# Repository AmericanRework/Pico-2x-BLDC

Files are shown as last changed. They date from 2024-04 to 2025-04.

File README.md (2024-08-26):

# Dual BLDC Controller
One RP2040 Pico drives two brushless motors! Uses SimpleFOC + Halls + TO-220 mosfets or IGBTs. Trying for low cost + lots of flexibility + solder it yourself at home + repairable. Works as a 3x DC motor controller as well.

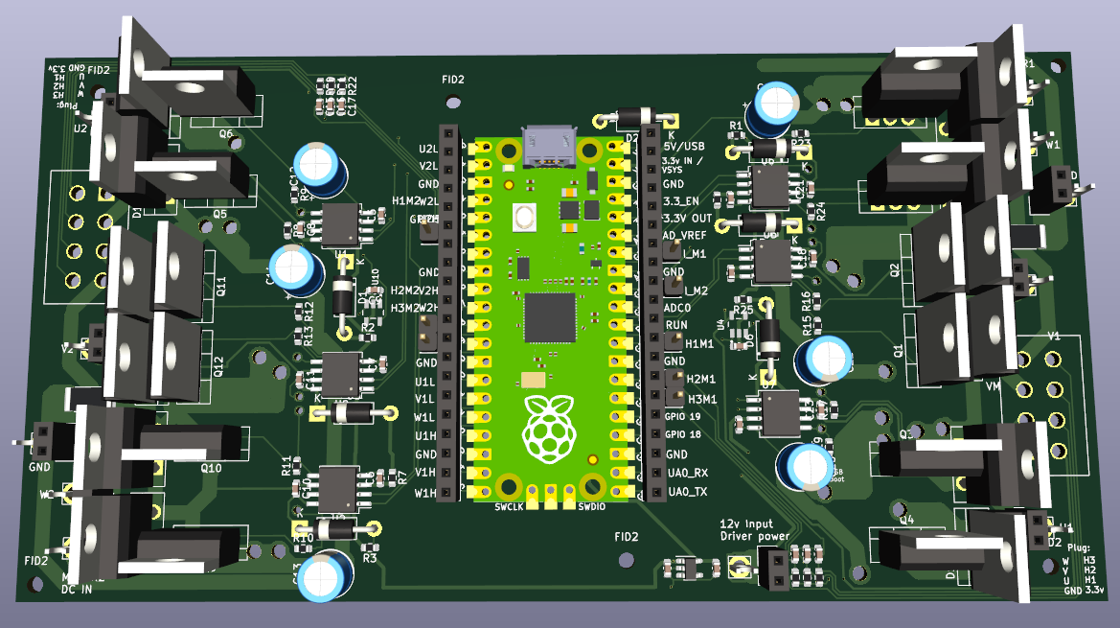
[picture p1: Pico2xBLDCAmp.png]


**Features:**

RP2040 Pico running Simplefoc (https://simplefoc.com/) and using halls (or -untested but should be possible- encoders) for motor commutation. (No FOC - RP2040 doesn't have enough A/D channels for 2x motor FOC.) Current sensing: 1 A/D channel and shunt resistor per motor. Uses 2304 half-H drivers. Can assemble only half the board if you only want one servo amp / want more pico I/O's. Spot for big diodes if you want 'em - Big motors seem to eat my mosfet body diodes rather quickly and IGBT's don't have body diodes. 

Control via usb serial or hardware serial. I2C, SPI, and software CAN might work but are untested. Serial is Human readable, following the simplefoc commander schema: AE1 enables motor, A10 sets motor A to 10 rev/sec, A0 stops motor A. AE0 quickly drops power to motor a. etc... B10 sets motor B to 10 rev/sec... etc... This allows you to control, test, and modify this servo amp right from the Arduino IDE or pretty much anything with a USB port or serial port.

Boards have a spot for molex plugs that are pin compatible with Husqvarna 450x automower drive motors. (NOT the cut motor - it's a different pinout but you can re-pin the cut motor - see additionalNotes.txt) 

Board requires your motor power DC source, and ~12vdc@ say 50mA. The board can either make 3.3v for the RP2040 pico, or you can provide external 3.3v. 

There's a very simple heartbeat signal in the code - if the amp doesn't get an instruction from serial it'll shut down, or delete that line to go forever!

**Assembly/Setup:**

Boards require SMD paste soldering and normal soldering to build: 

- SMD: It's not bad, order a solder mask when you order the board, place components, toaster oven for 3 mins. All SMD components are on the same side of the board. No tiny SMD stuff like the rp2040 chip itself - that's why we use a pico. All diodes are NOT SMD so you can tell which direction they go. (I can never see the tiny lines.) 
- Normal Soldering: in particular the mosfets. They are TO-220 because you are a hacker. You can solder in mosfets you have laying around and then de-solder them yourself to put better ones in. Or put in 3x0.1" pin headers so you can just plug in mosfets when you inevitably dead short them after trying to roll your own 3 phase driver. Basically you might want to 1. swap mosfets lots as you scratch write a 3phase driver. 2. use whatever mosfets are around. 3. repair it yourself. All of these would wreck a normal board but here you can just break out your trusty soldering iron and fix this board instead of throwing it in the trash!
- Make sure you order 2oz copper board so you get thick traces and can use higher current.

Assembled board:
plot

If you don't want to use the A/D (or want to repurpose any other inputs/outputs after you get a board) you can cut the trace to that pin(ehhh. update. not all the traces can be cut. is on hit list for next version), and there's a tinned hole for you to take over. And again, you don't have to build both servo amps if you want more IO's. 

'Firmware' for the rp2040 has some basic configuration and setup instructions in comments at the top of the code. It's pretty well tested and has been running on 2 boards for months without failing on an automower. Open up Arduino ide, install libraries: SimpleFOC, SimpleFOC drivers, and the Earle Philhower rp2040 core, compile and upload to your pico, good to go. Check top of the firmware file (RP2040SFocAmp.ino) for various additional documentation that might help you get started. 

There are two other firmware versions - one example for 3x DC motors, and one old version based on (https://github.com/ClemensElflein/xESC2040/tree/main/firmware/src) that does not use simplefoc. Both 'other' firmware versions need their pins.h file checked to be sure they follow the current board pico pin assignments, but should be somewhat functional other than that afaik. Let's call them good starting points. 

**Tested**

Tested using velocity control and torque control up to 10A/21v. You'll want heatsinks and low rdson mosfets to get to 10A. Tested the half-h drivers with igbts and better mosfets on a big inductive load to 60V, will update as we test more. Two boards are running in a Husqvarna 450x Automower as I write this. Maybe 10 hours of operation so far. Will update if/when anything fails. Update: ~100hrs of mowing, 0 servo amp faults/problems. Will still update if/when anything fails.

2 amps, 3 motors. One board has both drive motors, one has the cut motor.
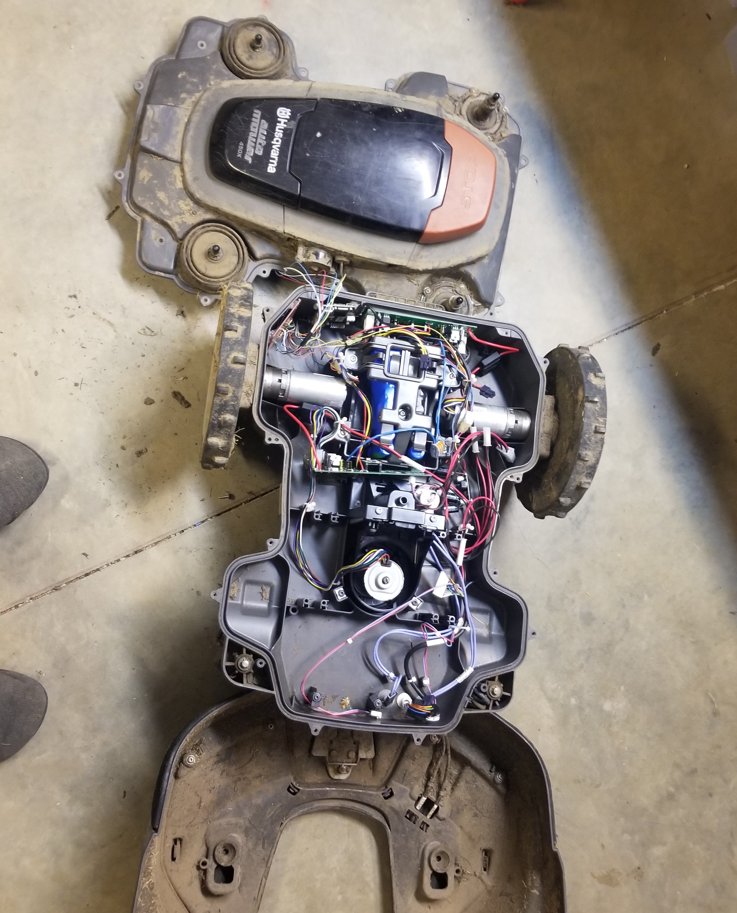
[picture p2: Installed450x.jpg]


Tested with 3x brushed (non 3 phase) motors using https://github.com/simplefoc/Arduino-FOC-dcmotor  - worked great but I did not test feedback, just that it could spin the motors. Off the top of my head there's only enough pico pins for 2x quadrature encoders.

**Thank you:**

Big thank you to https://github.com/ClemensElflein/ for creating the Open Mower project and his very well thought out 3 phase rp2040 servo amp code. His project inspired me to take the leap and make this happen. The original plan was use the openmower framework to control this servo amp, again - the amp plugs right into 450X automower drive motors, no hacking required. This board could(at least used to!) run (a version of?) the Xesc2040 servo amp code. Creating a firmware for this board that allows it to connect to openmower would be cool but I ended up writing a very simple mower controller instead.

SimpleFOC is absolutely brilliant. Can't recommend enough. If you are making bldc controllers they are a great place to start! (https://simplefoc.com/)

RP2040 / Pi Pico + Earle Philhower core (https://github.com/earlephilhower/arduino-pico) has been rock solid and a joy to work on. 

Thanks to everyone who open sources their work - makes the world a better place. Hope my code helps you!

**Plans/Stuff that's broken, rough order:**

- Current sense is at best not super calibrated, at worst needs work. Functions well enough to shut down the amp if current limit is hit.
- Test both DC and BLDC motors with an encoder instead of halls.
- Build more robots using this amp.
- Test it up to 240vdc/10A. Should work?
- When you disable a moving simplefoc motor with an 'AE0', it'll try to jump back to that velocity when you re-enable it. Might be fixed in newest simplefoc version or maybe it's something I did. Low priority 'cause it just spins a wheel a bit when you re-enable. Could be much a bigger problem on say a robot arm or CNC with a hard stop.
- Connect JUST the 2304's to a Mesa FPGA board running linuxCNC. Yep. Dump the pico and put your own brain on these drivers.
- I2C should work via pico pins GP17 and GP16. I think there is also now software CAN for the 2040 - loose 25% or so of one core but get CAN. Should be able to get it working. SPI is also exposed on pins 16/17/18/19 but again is untested. 

**Next board iteration:**

- Going to be a while. I've got enough of these boards for my next couple years of planned projects. Maybe...2027 or so we'll fix this stuff and anything else that shows up. Only thing that will trigger a sooner update is if high voltage or DC motor mode doesn't work.
- Heat sinks: Mosfet locations are not in a nice line. We've got 1 sink per mosfet, and once we start using more power we might want some real cooling here not just tiny heat sinks to air. Is it worth the pain of moving everything? Eh... Maybe. Might be easier to just machine the right pockets/holes into an aluminum block. 
- Delete the onboard 3.3v - Turns out you're not supposed to use linear regulators as DC-DC converters. Oops. It works but wastes 40mA+. Delete it 'cause 3.3v or 5v can come from RPi or BBB or pretty much any other board you use to drive this. AND if you have external 3.3v you can dump power to the pico even if you leave the DC main power connected.
- Redo pico io mapping so that each half-H is on it's own PWM slice.
- Motor 1 half-h cutable-traces: if you cut the top side trace between the pico and the tinned hole, remain connected to their half-h because traces went straight to the pico pins. 
- Make the power input and GND holes large enough to accommodate 12Ga wire.
- Fix various labels on the board. FID2 looking at you. Also most of the Motor 2 labels.

Cheers!
-American Rework

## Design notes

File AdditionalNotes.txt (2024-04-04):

Additional documentation:

To connect external 3.3v: use the 3.3v in / vsys pin (upper right corner of the pico if usb is top) It's labeled on the board.

Pinout for Husqvarna Automower 450x cut motor to match the drive motor 8 pin molex (drive motor comes with a 10 pin molex but only 8 pins used): 

-Plug latch on top. View looking at circuit board/back of plug:
-First row: black-gnd, blue-U, white-V, green-W
-Second row: red-3.3v, yellow-hallU, grey-hallV, purple-hallW

Gives same electrical angle as the drive motors. Our pinout is written directly on the board to make wiring up motors easy.

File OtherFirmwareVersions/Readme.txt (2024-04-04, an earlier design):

The RP2040BLDCAttempt2 firmware WILL NOT WORK on the current version of the board. Grab the new version of pins.h from the /firmware folder and you might be good. No promises though.

It is only an example/starting point if you want to roll your own servo amp and not use simplefoc. 

RP2040SimpleDC3xMTR has run 3x DC motors. Check the pins.h file just to be sure. I haven't tested it recently but it's probably ok. I have a project coming up where I need to control some DC motors so this might get updated in the next year or two. Heh.

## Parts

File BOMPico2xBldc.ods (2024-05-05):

Digikey Part # | Mfg Part # | Description | Qty | Cost | Line Cost | Notes | Total Cost
2648-SC0915CT-ND | SC0915 or SC0917 | Raspberry Pi Pico | 1 | 5 | 5 |  | 38.074
You Choose. |  | Power FET or IGBT | 12 | 0.87 | 10.44 | I have been quite happy with DMT6009LCT mosfets – Rdson 12mOhm, N-Channel 60 V 37.2A (Tc) 2.2W (Ta), 25W (Tc) Through Hole TO-220-3
 | SURF1060 | Big Flyback diode | 12 | 0.57 | 6.84 | Or try using mosfet body diodes. These have been pretty bulletproof so far: 10A / 600v.
DGD2304S8-13DICT-ND | DGD2304S8-13 | Gate driver | 6 | 1.2 | 7.2
RHM.001AUCT-ND | PMR100HZPFV1L00 | Current shunt resistor | 2 | 0.54 | 1.08
1276-1935-1-ND |  | .1uF SMD Cap | 14 | 0.018 | 0.252
1276-1062-1-ND |  | 470nF/16V Cap | 6 | 0.044 | 0.264 | boost caps – must upgrade for higher mains.
 |  | 2.2uF/400V | 6 |  | 0 | Mains caps
1276-1096-2-ND |  | 10uF/16V Cap | 2 | 0.1 | 0.2 | 1@ 12v and 1@ 3.3v
 | Diode:UF4007 | UF4007 Diode | 6 |  | 0
 | Diode:1N5817 | 1N5817 Shottkey Diode | 1 |  | 0
WM3583-ND | Molex 874270842 | Motor plug | 2 | 2.02 | 4.04 | Don't forget motor side of these and the pins.
 | Connector_PinSocket_2.54mm:PinSocket_1x20_P2.54mm_Vertical | Conn_01x20_Pin | 0 |  | 0 | Only if you are going to plug the pico in.
P10GCT-ND |  | 10 Resistor | 18 | 0.028 | 0.504
311-2.20KHRCT-ND |  | 2k2 Resistor | 6 | 0.019 | 0.114
696-1834-1-ND |  | 1mR Resistor | 2 | 0.67 | 1.34
296-47654-1-ND | INA180A3 | INA180A4 Currrent shunt Amplifier | 2 | 0.4 | 0.8
31-AP7383-33W5-7CT-ND |  | Unused: 3.3V Linear Regulator | 0 | 0.41 | 0 | Use external 3.3v so you can drop power to the pico remotely. Also, linear regulators aren't dc-dc buck converters lol....

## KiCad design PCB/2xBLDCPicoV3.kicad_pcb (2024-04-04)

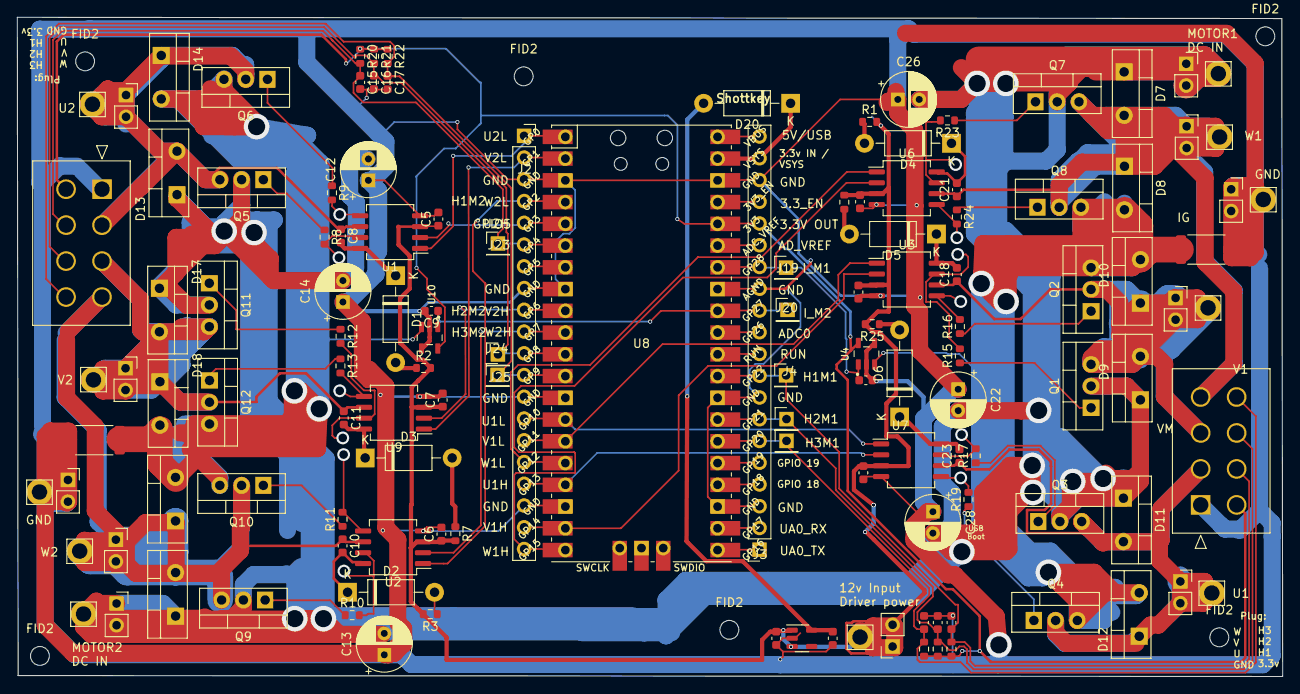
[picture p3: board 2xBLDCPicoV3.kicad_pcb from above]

Board: 4 copper layers, 147.8 x 77.0 mm, 124 parts (0 on the bottom side), 88 nets.

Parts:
C1, C5, C6, C7, C19, C27: 100nF; C_0603_1608Metric
C2, C3, C4, C9, C15, C16, C17, C20: .1uF; C_0603_1608Metric
C8, C10, C11, C18, C21, C23: 470nF/16V; C_0603_1608Metric
C12, C26: 2.2uF/400V; CP_Radial_D6.3mm_P2.50mm
C13, C14, C22, C28: 2.2uF/400v; CP_Radial_D6.3mm_P2.50mm
C24, C25: 10uF/16V; C_0603_1608Metric
D1, D2, D3, D4, D5, D6: UF4007; D_DO-41_SOD81_P10.16mm_Horizontal
D7, D8, D9, D10, D11, D12, D13, D14, D15, D16, D17, D18: C3D10060A; TO-220-2_Vertical
D20: 1N5817; D_DO-41_SOD81_P10.16mm_Horizontal
FID2, FID2#2, FID2#3, FID2#4, FID2#5, FID2#6: MTG Hole; MountingHole_2.2mm_M2
J1, J22: 874270842; CON_874270842
J2, J3: Conn_01x20_Pin; PinSocket_1x20_P2.54mm_Vertical
J4, J5, J7, J19, J20, J23, J24, J25: Conn_01x01_Pin; PinHeader_1x01_P2.54mm_Vertical
J6, J8, J9, J10, J11, J12, J13, J15, J16, J17, J18: Conn_01x02; PinSocket_1x02_P2.54mm_Vertical
Q1, Q2, Q3, Q4, Q5, Q6, Q11, Q12: IRF540N; TO-220-3_Vertical
Q7, Q8, Q9, Q10: STGP10NC60H; TO-220-3_Vertical
R1, R2, R3, R7, R8, R9, R10, R11, R12, R13, R15, R16, R17, R19, R23, R24, R25, R26: 010; R_0603_1608Metric
R4, R5, R6, R20, R21, R22: 2k2; R_0603_1608Metric
R14, R18: 1mR; R_2512_6332Metric
U1, U2, U3, U6, U7, U9: IRS2304; SO-8_5.3x6.2mm_P1.27mm
U4, U10: INA180A4; SOT95P280X145-5N
U5: XC6220B331MR; SOT-23-5
U8: Pico; RPi_Pico_SMD_TH

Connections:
+3V3: C25.1, D20.2 (A), U5.5 (VOUT)
+12V: C1.1, C5.1, C6.1, C7.1, C19.1, C24.1, C27.1, J11.1, J11.2, R1.2, R2.2, R3.2, R7.2, R25.2, R26.2, U1.3 (VCC), U2.3 (VCC), U3.3 (VCC), U5.1 (VIN), U5.3 (CE), U6.3 (VCC), U7.3 (VCC), U9.3 (VCC)
/+3.3V to Sensors: J1.5, J22.5, R4.1, R5.1, R6.1, R20.1, R21.1, R22.1
/HALL1: C2.1, J1.6, J4.1, R4.2
/HALL1M2: C15.1, J22.6, J23.1, R20.2
/HALL2: C3.1, J1.7, J5.1, R5.2
/HALL2M2: C16.1, J22.7, J24.1, R21.2
/HALL3: C4.1, J1.8, J7.1, R6.2
/HALL3M2: C17.1, J22.8, J25.1, R22.2
/MCU/+3.3V to Sensors: J3.16, U8.36 (3V3)
/MCU/ADCINSPARE1: J3.11, U8.31 (GPIO26_ADC0)
/MCU/CURRENT_SENSE: C20.1, J3.14, J19.1, U4.1 (OUT), U8.34 (GPIO28_ADC2)
/MCU/CURRENT_SENSEM2: C9.1, J3.12, J20.1, U8.32 (GPIO27_ADC1), U10.1 (OUT)
/MCU/HALL_1: J3.9, U8.29 (GPIO22)
/MCU/HALL_2: J3.7, U8.27 (GPIO21)
/MCU/HALL_2M2: J2.11, U8.11 (GPIO8)
/MCU/HALL_3: J3.6, U8.26 (GPIO20)
/MCU/HALL_3M2: J2.12, U8.12 (GPIO9)
/MCU/Hall_1_M2 / i2c0 SDA / UART1_TX: J2.6, U8.6 (GPIO4)
/MCU/Spare1/spi0 TX/i2c1 SCL: J3.5, U8.25 (GPIO19)
/MCU/Spare2/spi0 SCK/i2c1 SDA: J3.4, U8.24 (GPIO18)
/MCU/Spare3 / i2c0 SCL UART1_RX: J2.7, U8.7 (GPIO5)
/MCU/U1H: J2.17, U7.2 (HIN), U8.17 (GPIO13)
/MCU/U1L: J2.14, U7.1 (LIN), U8.14 (GPIO10)
/MCU/U2H: J2.5, U1.2 (HIN), U8.5 (GPIO3)
/MCU/U2L: J2.1, U1.1 (LIN), U8.1 (GPIO0)
/MCU/UART0_RX /spi0 Csn / I2C0 SCL: J3.2, U8.22 (GPIO17)
/MCU/UART0_TX /spi0 RX / I2C0 SDA: J3.1, U8.21 (GPIO16)
/MCU/V1H: J2.19, U3.2 (HIN), U8.19 (GPIO14)
/MCU/V1L: J2.15, U3.1 (LIN), U8.15 (GPIO11)
/MCU/V2H: J2.9, U8.9 (GPIO6), U9.2 (HIN)
/MCU/V2L: J2.2, U8.2 (GPIO1), U9.1 (LIN)
/MCU/W1H: J2.20, U6.2 (HIN), U8.20 (GPIO15)
/MCU/W1L: J2.16, U6.1 (LIN), U8.16 (GPIO12)
/MCU/W2H: J2.10, U2.2 (HIN), U8.10 (GPIO7)
/MCU/W2L: J2.4, U2.1 (LIN), U8.4 (GPIO2)
/PowerM1/HSW: R23.2, U6.7 (HO)
/PowerM1/IGBT_GND: D8.2 (A), D10.2 (A), D12.2 (A), Q2.3 (S), Q4.3 (S), Q8.3 (S), R18.1, U4.3 (IN+)
/PowerM1/LSW: R24.2, U6.5 (LO)
/PowerM2/HSW: R10.2, U2.7 (HO)
/PowerM2/IGBT_GND: D14.2 (A), D16.2 (A), D18.2 (A), Q6.3 (S), Q10.3 (S), Q12.3 (S), R14.1, U10.3 (IN+)
/PowerM2/LSW: R11.2, U2.5 (LO)
/PowerM2/U_To_PlugM2: C8.1, D13.2 (A), D14.1 (K), J18.1, J18.2, Q5.3 (S), Q6.2 (D), U1.6 (VS)
/PowerM2/VM2: C12.2, C13.2, C14.2, D13.1 (K), D15.1 (K), D17.1 (K), J15.1, J15.2, Q5.2 (D), Q9.2 (D), Q11.2 (D)
/PowerM2/V_To_PlugM2: C11.1, D17.2 (A), D18.1 (K), J17.1, J17.2, Q11.3 (S), Q12.2 (D), U9.6 (VS)
/PowerM2/W_To_PlugM2: C10.1, D15.2 (A), D16.1 (K), J16.1, J16.2, Q9.3 (S), Q10.2 (D), U2.6 (VS)
/U_To_Plug: C23.1, D11.2 (A), D12.1 (K), J1.2, J9.1, J9.2, Q3.3 (S), Q4.2 (D), U7.6 (VS)
/VM: C22.2, C26.2, C28.2, D7.1 (K), D9.1 (K), D11.1 (K), J10.1, J10.2, Q1.2 (D), Q3.2 (D), Q7.2 (D)
/V_To_Plug: C18.1, D9.2 (A), D10.1 (K), J1.3, J6.1, J6.2, Q1.3 (S), Q2.2 (D), U3.6 (VS)
/W_To_Plug: C21.1, D7.2 (A), D8.1 (K), J1.4, J8.1, J8.2, Q7.3 (S), Q8.2 (D), U6.6 (VS)
GND: C1.2, C2.2, C3.2, C4.2, C5.2, C6.2, C7.2, C9.2, C12.1, C13.1, C14.1, C15.2, C16.2, C17.2, C19.2, C20.2, C22.1, C24.2, C25.2, C26.1, C27.2, C28.1, J1.1, J2.3, J2.8, J2.13, J2.18, J3.3, J3.8, J3.13, J3.18, J12.1, J12.2, J13.1, J13.2, J22.1, R14.2, R18.2, U1.4 (COM), U2.4 (COM), U3.4 (COM), U4.2 (GND), U4.4 (IN-), U5.2 (GND), U6.4 (COM), U7.4 (COM), U8.3 (GND), U8.8 (GND), U8.13 (GND), U8.18 (GND), U8.23 (GND), U8.28 (GND), U8.33 (AGND), U8.38 (GND), U9.4 (COM), U10.2 (GND), U10.4 (IN-)
unnamed: D1.2 (A), R2.1
unnamed: C8.2, D1.1 (K), U1.8 (VB)
unnamed: D2.2 (A), R3.1
unnamed: C10.2, D2.1 (K), U2.8 (VB)
unnamed: D3.2 (A), R7.1
unnamed: C11.2, D3.1 (K), U9.8 (VB)
unnamed: D4.2 (A), R1.1
unnamed: C21.2, D4.1 (K), U6.8 (VB)
unnamed: D5.2 (A), R26.1
unnamed: C18.2, D5.1 (K), U3.8 (VB)
unnamed: D6.2 (A), R25.1
unnamed: C23.2, D6.1 (K), U7.8 (VB)
unnamed: D20.1 (K), J3.19, U8.39 (VSYS)
unnamed: J3.10, U8.30 (RUN)
unnamed: J3.15, U8.35 (ADC_VREF)
unnamed: J3.17, U8.37 (3V3_EN)
unnamed: J3.20, U8.40 (VBUS)
unnamed: Q1.1 (G), R15.1
unnamed: Q2.1 (G), R16.1
unnamed: Q3.1 (G), R17.1
unnamed: Q4.1 (G), R19.1
unnamed: Q5.1 (G), R8.1
unnamed: Q6.1 (G), R9.1
unnamed: Q7.1 (G), R23.1
unnamed: Q8.1 (G), R24.1
unnamed: Q9.1 (G), R10.1
unnamed: Q10.1 (G), R11.1
unnamed: Q11.1 (G), R12.1
unnamed: Q12.1 (G), R13.1
unnamed: R8.2, U1.7 (HO)
unnamed: R9.2, U1.5 (LO)
unnamed: R15.2, U3.7 (HO)
unnamed: R16.2, U3.5 (LO)
unnamed: R17.2, U7.7 (HO)
unnamed: R19.2, U7.5 (LO)
unnamed: R12.2, U9.7 (HO)
unnamed: R13.2, U9.5 (LO)

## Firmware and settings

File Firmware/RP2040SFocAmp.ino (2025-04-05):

/*
** Most recent version as of March 2024. Servo amp for Automower!
This is mostly example code from SimpleFOC. Follow their license. 

DO NOT PLUG PICO INTO USB WHILE IT'S INSTALLED /PLUGGED INTO BEAGLEBONE. WILL SEND POSSIBLY 5V DOWN THE BEAGLEBONE 3.3V POWER LINE.

Install: 
use Arduino ide, add packages / boards:
known working:
Simplefoc 2.3.2, SimpleDCmotor 1.0.0 simplefocDrivers 1.0.6, board: Raspi pico rp2040 by Philhower 3.7.2
Testing:
SimpleDCmotor 1.0.2 simplefocDrivers 1.0.7

HAD TO delete rp2040.h under current sense in the standard simplefoc library to get this pwm on rp2040 to work... 2024: No longer have to do this!

future self: to get serial access in linux: usermod -a -G tty myusername
and possibly: sudo gpasswd --add ${USER} dialout


Downloading to a pico:
plug in, check show all devices, look for uf2 devices - may have to select the board type - a rp2040 pico not the mbed version.

Running it:
  to 'command' use ? to list commands. not that useful. but then you can say "AE0" to disable motor A, AE1 ENABLES. 
  A10: 10 Is like set torqe/velocity goal to 10. YEP. STARTING AT 1 OR EVEN LESS IS A GOOD IDEA.

//commander is set to have some extra methods: I, C, H, and V all do extra stuff we add here. Check out commander.h for more stuff you can do!
// I is (re)-init. I still can't get init to run a full alignment cycle but can force various override angles? Probably could fix but just never end up using it.
//C is measure current? I think? 
//H is hall state. Helpful when you are adding halls to a non-hall motor.
//V is current velocity. 
 */

 //motors are currently set to use velocity control - and hopefully negative values go in reverse? we'll see.
 //CONFIRMED! NEGATIVE VELOCITY IS CHANGE DIRECTION. WOO0.

//not sure what happened one time I tried sending A10 B10 and b motor just stopped working. reboot fixed lol...
//YO THIS IS IMPORTANT: Can set to use heartbeat or usb/ hardware serial ports. See below.


//#include <Arduino.h>
#include <SimpleFOC.h>
// software interrupt library
//#include <PciManager.h>
//#include <PciListenerImp.h>
#include <SimpleFOCDrivers.h>
#include "pins.h"


//motor pole pairs = # of permanent magnets in rotor.
BLDCMotor motor = BLDCMotor(11);

BLDCMotor motor2 = BLDCMotor(11);
//BLDCDriver3PWM driver = BLDCDriver3PWM(9, 5, 6, 8);

BLDCDriver6PWM driver = BLDCDriver6PWM(PIN_UH, PIN_UL, PIN_VH, PIN_VL, PIN_WH, PIN_WL);

BLDCDriver6PWM driver2 = BLDCDriver6PWM(PIN_UHM2, PIN_ULM2, PIN_VHM2, PIN_VLM2, PIN_WHM2, PIN_WLM2);

// Stepper motor & driver instance
//StepperMotor motor = StepperMotor(50);
//StepperDriver4PWM driver = StepperDriver4PWM(9, 5, 10, 6,  8);

// hall sensor instance
HallSensor sensor = HallSensor(PIN_HALL_U, PIN_HALL_V, PIN_HALL_W, 11);

int hallu, hallv, hallw = 0; //for manual hall testing.

HallSensor sensor2 = HallSensor(PIN_HALL_UM2, PIN_HALL_VM2, PIN_HALL_WM2, 11);
// Interrupt routine intialisation
// channel A, B and C callbacks


//////////////////////////////////////////////////////////////////////////////////////////
// YO THESE ARE IMPORTANT. SET THEM APPROPRIATELY SO THAT WE ONLY HAVE TO MAINTAIN ONE SERVOAMP CODEBASE.
HardwareSerial* whichSerial = &Serial1; //&Serial for usb or &Serial1 for hardware pins. See pins.h for which pins to use. &Serial2 Should also work but is untested.


//heartbeat:
bool useHeartbeat = true; //true to turn everything off if we dont' hear from coms. 
unsigned long last_heartbeat_millis = 0;
int heartbeat_shutdown_millis = 5000; // 5000 ms = 5 seconds no instruction shut down motors. Yes that's kind of a long time. meh. at least it's there.


void doA(){sensor.handleA();}
void doB(){sensor.handleB();}
void doC(){sensor.handleC();}

void doA2(){sensor2.handleA();}
void doB2(){sensor2.handleB();}
void doC2(){sensor2.handleC();}

//first # is milivolts per ... amp? 
//InlineCurrentSense the_current_sense = InlineCurrentSense(500.0, PIN_CURRENT_SENSE, PIN_CURRENT_SENSE);
//DIY that shit:
float motor1_Current = 0;
float motor1_AvgCurrent = 0;
int debugCounter = 0;

float motor2_Current = 0;
float motor2_AvgCurrent = 0;

// commander interface
//there are zero - ZERO! examples of two motors controlled by the commander. wut!? Maybe I bad at searching. this should be interesting.
// I got AI to spit out an example it claims will send the same command to both motors. ugh. not what I need.
Commander command = Commander(*whichSerial);
void onMotor(char* cmd){ command.motor(&motor, cmd); }
void onMotor2(char* cmd){ command.motor(&motor2, cmd); }

//try to restart a motor? doesn't quite work right. 
void reInit1(char* cmd){ 
  /*
  motor.init();
  motor.target = 0; //wish this was to CMD then you could init @ different power levels woo.
  motor.enable();
  //motor.initFOC(); //this doesn't force a re-align for some reason...
  motor.initFOC(5.236, Direction::CCW);
  */
   }

//OK! after some testing, sampling every loop and adding to a moving average: 
//0 reads 4-10, 0.5 amps reads 165 to 175, 1.5 amps reads 370 to 390, ~ 10A 912-933, ~4 AMPS 616 TO 703.
void readCurrent(char* cmd){ 
  //motor1_Current = the_current_sense.getDCCurrent();
 // motor1_Current = analogRead(PIN_CURRENT_SENSE);
//  *whichSerial.println(motor1_Current);

    whichSerial->println(motor1_AvgCurrent);
    whichSerial->println(motor2_AvgCurrent);
 }

 void printVelo(char* cmd){ 
  whichSerial->println(motor.shaft_velocity);
  whichSerial->println(motor2.shaft_velocity);
 }

void readHalls(char* cmd){ 
  hallu = digitalRead(PIN_HALL_U);
  hallv = digitalRead(PIN_HALL_V);
  hallw = digitalRead(PIN_HALL_W);
  whichSerial->println("HALLS:");
  whichSerial->println(hallu);
  whichSerial->println(hallv);
  whichSerial->println(hallw);
 }



void setup() {

  // initialize encoder sensor hardware
  
  sensor.init();
  sensor.enableInterrupts(doA, doB, doC);
  
   
  sensor2.init();
  sensor2.enableInterrupts(doA2, doB2, doC2);
  


  //COMMENT THIS OUT TOO FOR OPEN LOOP!
  motor.linkSensor(&sensor);

  motor2.linkSensor(&sensor2);


  //CURRENT SENSOR - sfoc version. Doesn't 'just work.' doing my own thing but I'll leave this here maybe help someone. 
  //inlineCurrentSense(resistorValue,gain,AnalogPin#'s) or (mv/amp, analogpins)
  //the_current_sense = InlineCurrentSense(200.0, PIN_CURRENT_SENSE, PIN_CURRENT_SENSE);
  
  //the_current_sense.init();
  // do this not sure if it'll break motor alignment ability:  motor.linkCurrentSense(&current_sense);

  // link current sense and driver
  //current_sense.linkDriver(&driver);
  // link motor and current sense
  //motor.linkCurrentSense(&current_sense);


  //should be able to do this to get DC current:
  //  motor1_Current = current_sense.getDCCurrent();




  // driver config
  // power supply voltage [V]
  driver.voltage_power_supply = 12;
  driver.init();
  driver.dead_zone = 0.1;
  // link driver
  motor.linkDriver(&driver);

  driver2.voltage_power_supply = 12;
  driver2.init();
  driver2.dead_zone = 0.1;
  // link driver
  motor2.linkDriver(&driver2);



  // choose FOC modulation OPEN LOOP TO TEST A MOTOR? SEE THE BLDC ATTEMPT #5 FOR WORKING OPEN LOOP
 // motor.foc_modulation = FOCModulationType::SinePWM;
  // set control loop type to be used
 //motor.controller = MotionControlType::velocity_openloop;

 
 motor.phase_resistance = 1.8;
 motor.current_limit = 3.0;
 motor.KV_rating = 100; //RPM'S PER VOLT! THE MISSING LINK! WHO KNOWS WHAT IT DEFAULTED TO BUT NOW IT CAN GO FASTER COOL. 
 //if motor kv and phase resistance are set, simplefoc will try to follow rough guess at current_limit.


 motor2.phase_resistance = 1.8;
 motor2.current_limit = 3.0;
 motor2.KV_rating = 100;


 //Open loop? see above. 
 motor.foc_modulation = FOCModulationType::SpaceVectorPWM;
  motor.controller = MotionControlType::velocity;
//Don't forget to uncomment above sensor link

 motor2.foc_modulation = FOCModulationType::SpaceVectorPWM;
  motor2.controller = MotionControlType::velocity; 


  // contoller configuration based on the controll type
  motor.PID_velocity.P = 0.01f; // was 0.05f
  motor.PID_velocity.I = 0.2; //WAS 20
  motor.PID_velocity.D = 0;
  // default voltage_power_supply
  motor.voltage_limit = 20.0;
  // velocity low pass filtering time constant
  motor.LPF_velocity.Tf = 0.01f;
  // angle loop controller
  motor.P_angle.P = 0;
  // angle loop velocity limit. WAS 15 IS THIS # IN HZ? YES IT IS! WHY DO CS PEOPLE NEVER DO UNITS?
  motor.velocity_limit = 25;

//////////////////////////////M2!! tempted to comment this all out but let's see if straight copy works first. 
  motor2.PID_velocity.P = 0.01f; // was 0.2f
  motor2.PID_velocity.I = 0.2; //WAS 20
  motor2.PID_velocity.D = 0;
  motor2.voltage_limit = 20.0;
  motor2.LPF_velocity.Tf = 0.01f;
  motor2.P_angle.P = 0;
  motor2.velocity_limit = 25;

  

  // start monitoring / commander serial port.
  if(whichSerial == &Serial1){
    Serial1.setRX(PIN_SERIAL1_RX);
    Serial1.setTX(PIN_SERIAL1_TX);
    Serial1.begin(115200);
  }
  else{
    Serial.begin(115200);
  }
  // comment out if not needed
  motor.useMonitoring(*whichSerial);
  motor2.useMonitoring(*whichSerial);

  // initialise motor
  motor.init();

  motor2.init();
 


  // define the motor id (WHAT THIS IS NOT DEFINING A MOTOR ID IT'S LINKING THE SERIAL PORT TO THE MOTOR THRU THE ONMOTOR METHOD YA?)
  command.add('A', onMotor, "motor");
  command.add('B', onMotor2, "motor2");
  command.add('I', reInit1, "restart motor1");
  command.add('C', readCurrent, "current of motor1");
  command.add('H', readHalls, "digitalRead hall u,v,w");
  command.add('V', printVelo, "pls work - want velocity");


  // set the inital target value
  motor.target = 0;
  motor.enable();

  motor2.target = 0;
  motor2.enable();

  // align encoder and start FOC - this will move the motors to find the electrical angle.
  //motor.initFOC();
  //motor2.initFOC();

  //once you get the alignment, use this:
  motor.sensor_direction=Direction::CCW; // or Direction::CW
  motor.zero_electric_angle=5.24;     // use the real value!


  motor2.sensor_direction=Direction::CCW; // or Direction::CW
  motor2.zero_electric_angle=5.24;     // use the real value!

  /* why they screw up perfect system!?
   motor.initFOC(5.24, Direction::CCW); 
   motor2.initFOC(5.24, Direction::CCW); 
*/
motor.initFOC();
motor2.initFOC();

  // Run user commands to configure and the motor (find the full command list in docs.simplefoc.com)
  whichSerial->println(F("wooooooooooooooooooooo 2 motors."));

  _delay(1000);
}


void loop() {
  

  // iterative setting FOC phase voltage
  motor.loopFOC();

 // motor2.loopFOC();

  motor.move();

 // motor2.move();
/* This stuff is in the other core of the rp2040 'cause there was a bug with pwm and hardware serial. Or put it back here if you want.

  //heartbeat:
  if(whichSerial->available()){
    last_heartbeat_millis = millis();
  }
  else if (useHeartbeat && (last_heartbeat_millis + heartbeat_shutdown_millis <  millis())){
    //shutdown!
    motor.target = 0;
    motor2.target = 0;
  }
  // user communication
  command.run();

*/
  //custom adds:
  motor1_Current = analogRead(PIN_CURRENT_SENSE);
  motor1_AvgCurrent = (motor1_AvgCurrent + (motor1_Current * 0.001))/1.001;
  motor2_Current = analogRead(PIN_CURRENT_SENSEM2);
  motor2_AvgCurrent = (motor2_AvgCurrent + (motor2_Current * 0.001))/1.001;

  if(debugCounter > 100) {
//  motor1_Current = the_current_sense.getDCCurrent();
  //motor1_Current = analogRead(PIN_CURRENT_SENSE);
  //motor1_AvgCurrent = (motor1_AvgCurrent + (motor1_Current * 0.001))/1.001;
  //zero motor if current is high
  if((motor1_AvgCurrent > 800) or (motor2_AvgCurrent > 800))
  {
      motor.target = 0;
      motor2.target = 0;
      motor.disable();
      motor2.disable();
      whichSerial->print("OVERCURRENT! ");
      //whichSerial->println(motor1_Current);
  }
  //whichSerial->println(motor1_Current);
  debugCounter = 0;
  }
  debugCounter++;

}

void loop1() {

  motor2.loopFOC();

  motor2.move();
  //heartbeat:
  if(whichSerial->available()){
    last_heartbeat_millis = millis();
  }
  else if (useHeartbeat && (last_heartbeat_millis + heartbeat_shutdown_millis <  millis())){
    //shutdown!
    motor.target = 0;
    motor2.target = 0;
  }
  // user communication
  command.run();

}

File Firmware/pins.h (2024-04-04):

#pragma once

#define PIN_UH 13
#define PIN_VH 14
#define PIN_WH 15
#define PIN_UL 10
#define PIN_VL 11
#define PIN_WL 12
#define PIN_UHM2 3
#define PIN_VHM2 6
#define PIN_WHM2 7
#define PIN_ULM2 0
#define PIN_VLM2 1
#define PIN_WLM2 2
#define PIN_CURRENT_SENSE 28
#define PIN_CURRENT_SENSEM2 27


#define PIN_HALL_U 22
#define PIN_HALL_V 21
#define PIN_HALL_W 20
#define PIN_HALL_UM2 4
#define PIN_HALL_VM2 8
#define PIN_HALL_WM2 9

#define PIN_SERIAL1_TX 16
#define PIN_SERIAL1_RX 17

//#define PIN_SERIAL2_TX (8u)
//#define PIN_SERIAL2_RX (9u)

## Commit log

2024-04-04 Picture of amp + Husqvarna mower motor
2024-04-04 Delete AssembledDualBLDCController.jpg
    Holy F*** If you can't make a web interface why would I let you install a script on my machine? And if you made a web interface that worked, I wouldn't need a script in the first place!
2024-04-04 BOM done! Crossed off todo list.
2024-05-05 qty was wrong
    [BOMPico2xBldc.ods]

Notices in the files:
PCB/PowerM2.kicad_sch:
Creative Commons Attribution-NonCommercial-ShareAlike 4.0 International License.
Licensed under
